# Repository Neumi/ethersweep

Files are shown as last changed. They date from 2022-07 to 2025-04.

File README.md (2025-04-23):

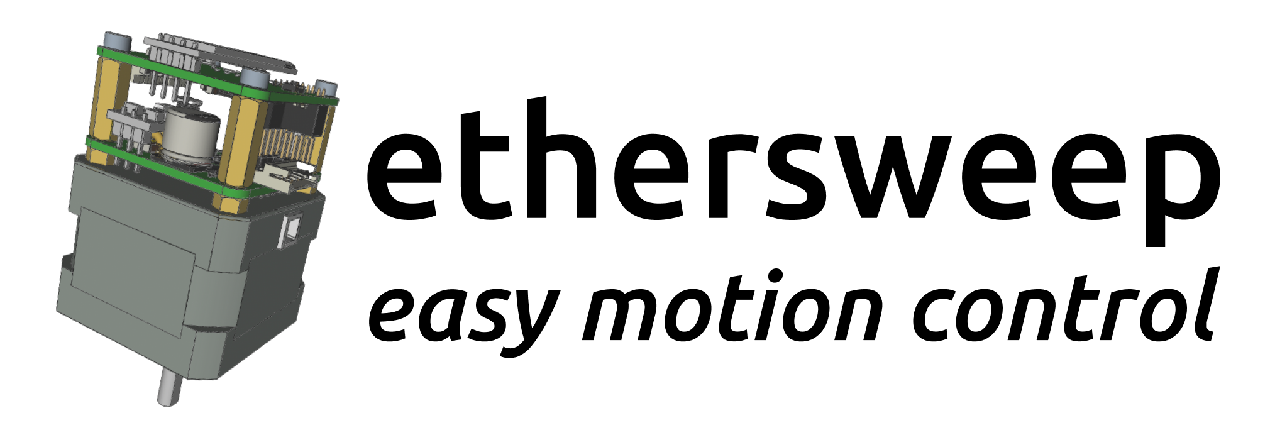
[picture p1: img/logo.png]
Ethersweep Logo


# Ethersweep
### An Open Source Ethernet controllable stepper motor. Easy interfacing with JSON and UDP from any device on the network in any language you choose.

Want to stay updated or participate? Join my [Discord](https://discord.com/invite/rerCyqAcrw)!

*As there is quite some interest in buying a controller, please fill out this form to help me better understand what Ethersweep would be used for https://forms.gle/FLgfvCP1hjCCp2636*

More media/press material:
https://drive.google.com/drive/folders/1qrk8QeEkzJ8hkr-H0x3y7xxhLTKhMb_F?usp=share_link

> *NEWS NOTE:*  Ethersweep is a project still in development. If you plan to order boards for yourself, you can, but expect it to take some work to get everything running! If you have any questions, please write me on Discord: https://discord.com/invite/rerCyqAcrw or
LinkedIn: https://www.linkedin.com/in/neumi/
If you need a custom assembly code or have a special use case in mind, contact me.
The latest running version is in the [production](electronic_design/production) directory. It is now an STM32f103 version with TMC2209 stepper driver. The assembly files contain LCSC part numbers and can be directly ordered at JLCPCB including assembly. Only some THT parts and SMD AS5600 encoder must be soldered by hand.

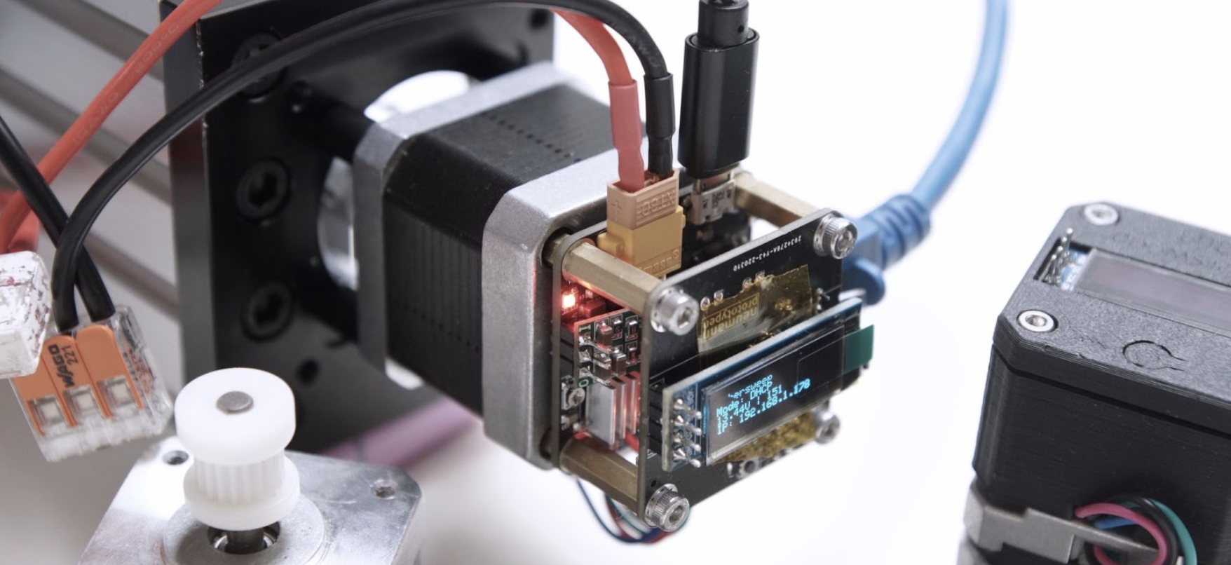
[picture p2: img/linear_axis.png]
linear axis


## What it does
Ethersweep is a motor controller for NEMA17 stepper motors that can be controlled from normal Ethernet networks. This means that you will be able to control motion from normal computers (laptop/server/raspberrypi), mobile devices, microcontrollers, PLCs and any other machine that is capable of sending UDP messages. On top you can control as many motors as you like because every motor gets an IP address from the DHCP server on your network.
You can also connect End and E-Stops to the controller. Sensor data like encoder feedback, voltage, running and button states can also be requested via network requests.

All you need is a network and power between 5v and 30v.
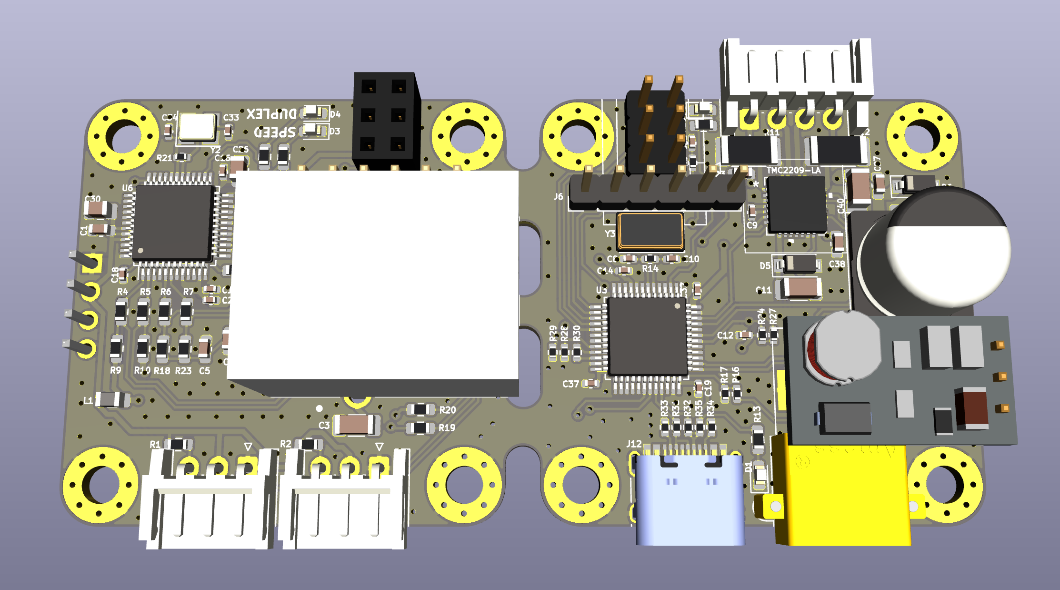
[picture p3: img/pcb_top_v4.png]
PCB Photo


## What it needs
Every motor has to be connected to an Ethernet network (optimally with DHCP) and a power supply between 5...30V. USB can be used for programming the controller with new firmware. End and E-Stops can be connected with JST3-pin connectors. To send instructions to Ethersweep you just send a JSON-encoded message via UDP to the controller's IP and port.

## Features:
- W5500 Ethernet controller
- STM32f103 Microcontroller @ 72MHz
- Trinamic TMC2209 Stepper motor driver
- AS5600 magnetic rotary encoder
- XT30 power connector
- Oled 128x32 Display
- USB programmable
- Inputs for E-Stop and End-Stop
- Reset button
- Fits on a NEMA17 stepper motor
- standard RJ45 network connector

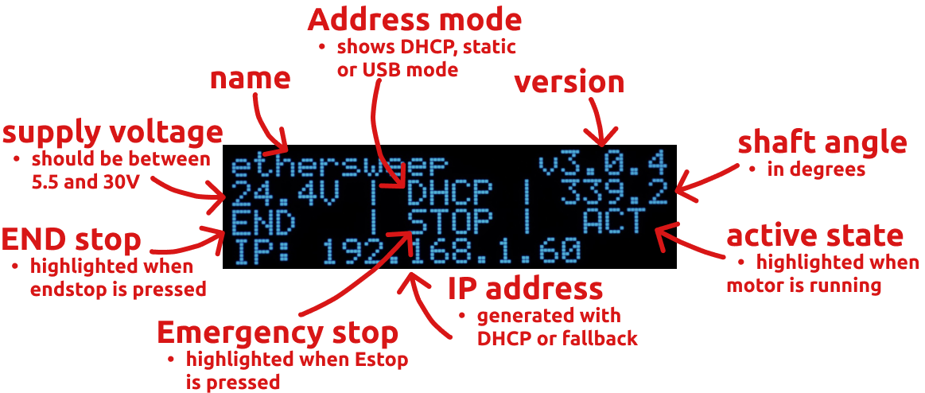
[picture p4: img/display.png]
Display content


## How to get started:
Build an (or multiple) Ethersweep controller. All manufacturing/assembly files work with JLCPCB and only some easy THT soldering is needed when the boards arrive. The code is available in the repository.

Connect your Ethersweep controller to your network via ethernet and connect to a 5.5...30V power source. Stick an encoder magnet (radial magnetized) on a NEMA17 motor shaft and connect the controller to the four M3 screws of the motor.
Once connected to power and Ethernet, it searches for an IP address using DHCP. When an IP is found, the controller shows it on the display and it's ready to use. When no IP is found, it defaults to 192.168.1.111 if available. (It is recommended to use DHCP)

Now you can use the Python script to control the motor.

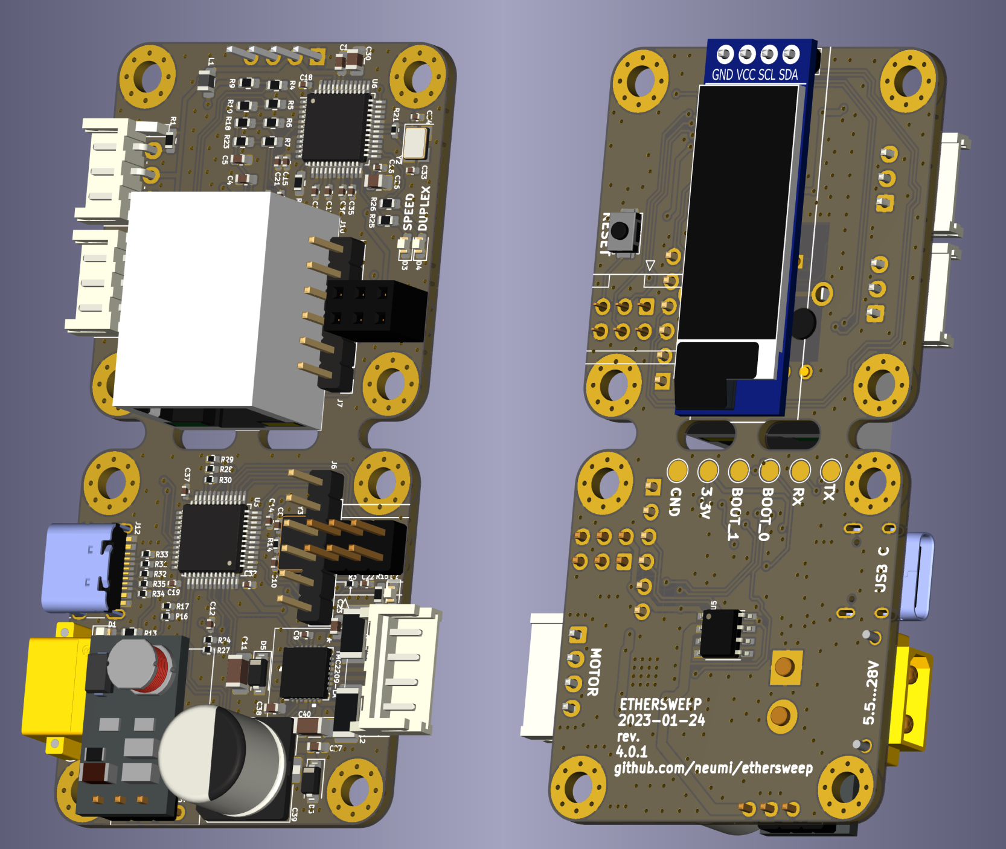
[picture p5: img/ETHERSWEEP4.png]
PCB raw B

cad rotation
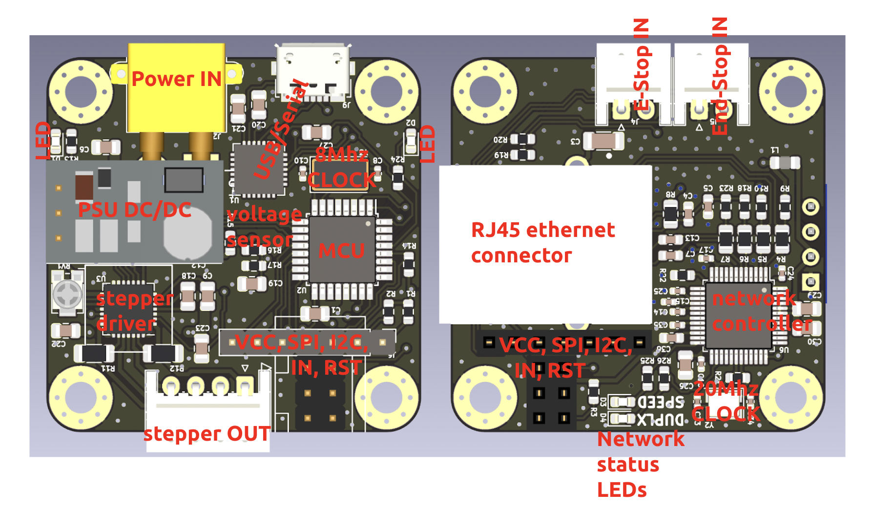
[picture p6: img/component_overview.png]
pcb layout


## Using Python to control a stepper motor:

```python
import socket
import json

IP_MOTOR = "192.168.1.185" # ethersweep IP (change to motors IP)
UDP_PORT = 8888 # ethersweep port

def drive_motor(steps, speed, direction, mode, motor_ip):
    json_data = json.dumps({'steps': steps, 'speed': speed, 'direction': direction, 'mode': mode})
    message = json_data.encode()
    sock = socket.socket(socket.AF_INET, socket.SOCK_DGRAM)
    sock.sendto(message, (motor_ip, UDP_PORT))

drive_motor(100, 9500, 1, 32, IP_MOTOR) # this will spin the motor 100 steps
```

## Video:
LINK TO VIDEO (https://www.youtube.com/watch?v=80j7L1H61Hw)

Follow the project on hackaday.io: https://hackaday.io/project/187187-ethersweep

## Upcoming Features:
- [ ] improved Broadcast mode + motor synchronization for multiple motors
- [ ] motor servo mode
- [ ] TMC2209 software interface
- [ ] scheduler

## Big thanks to the sponsors of this project!
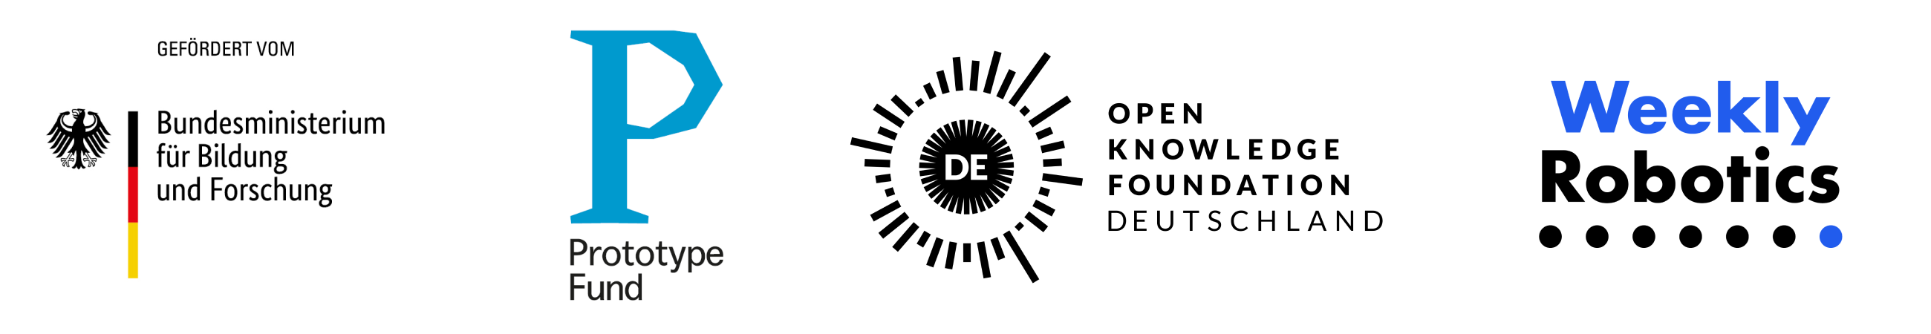
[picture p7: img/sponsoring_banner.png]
sponsor_banner


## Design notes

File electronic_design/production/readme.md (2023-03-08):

# Production ready files

If you like to build an Ethersweep version, check these folders. All versions in this folder are checked and can be ordered from a PCB manufacturer.

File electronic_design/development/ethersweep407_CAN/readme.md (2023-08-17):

# Version 4.6.0

Current development files.

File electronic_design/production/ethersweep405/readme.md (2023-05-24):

# Version 4.5.0

Added CP2102 with STM32f103 and micro USB on a four layer board.
Sent to manufacturing on 24.05.2023

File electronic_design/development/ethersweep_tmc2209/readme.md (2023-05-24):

# Ethersweep with TMC2209

This versions goal was to fix some issues I had with the Atmega328 / TMC2208 version.
I changed:
  - STM32f103 at 72Mhz instead of ATMega328 at 8Mhz
  - native USB support instead of CP2102 serial/USB converter
  - USB C connector instead of Micro USB
  - TMC2209 instead of TMC2208 (Sensorless homing!!, higher current, faster speeds, software interface)
  - 3-pin (3.3,gnd,sig) HOME and ESTOP connectors instead of 2-pin
  - better power design -> less noise

Unfortunately, I made two pretty annoying mistakes. Therefore Ethersweep was not working (old verion 3 boards could be used though) and the TMC2209 didn't work as well. Accordingly this is not a production version. The issues will be fixed in Version 4.2.0.

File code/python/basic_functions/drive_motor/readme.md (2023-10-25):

### Basic Drive Motor Command

Run this command to get an Ethersweep controller spinning. This is a very basic test to run the motor a certain amounts of steps in a certain direction with a certain speed with the option to hold or freewheel the motor in the end.

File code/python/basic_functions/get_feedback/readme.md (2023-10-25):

### Get feedback from Ethersweep

This triggers the Ethersweep controller to send back feedback like voltage, angle and other parameters. It is an asynchronous setup. One is sending requests, the other task receives the feedback from the controller.

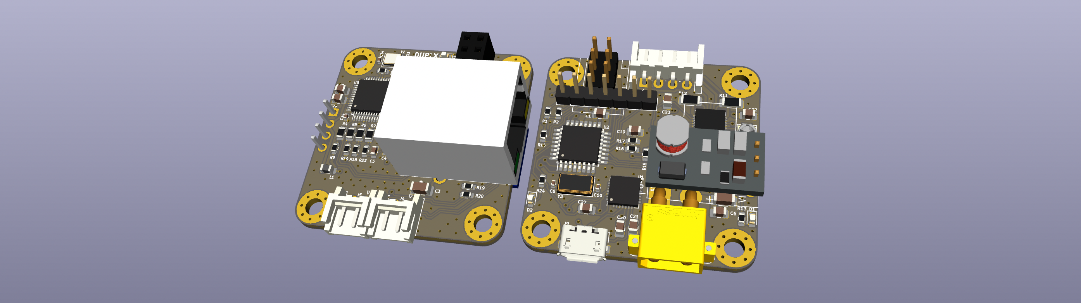
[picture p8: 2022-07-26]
img/3d_side.png

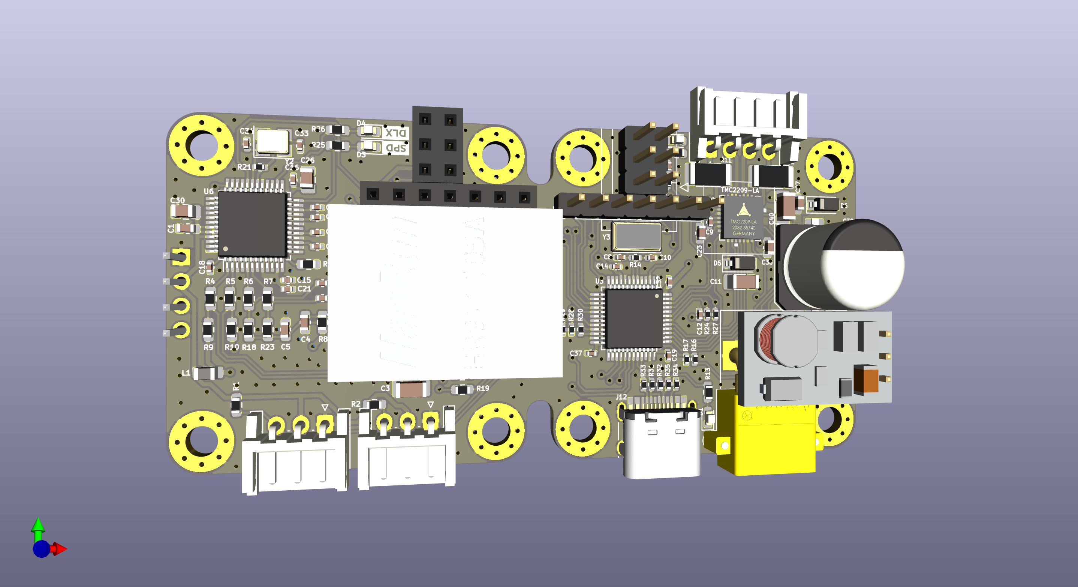
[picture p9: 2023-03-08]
img/rotation/ethersweep_2.png

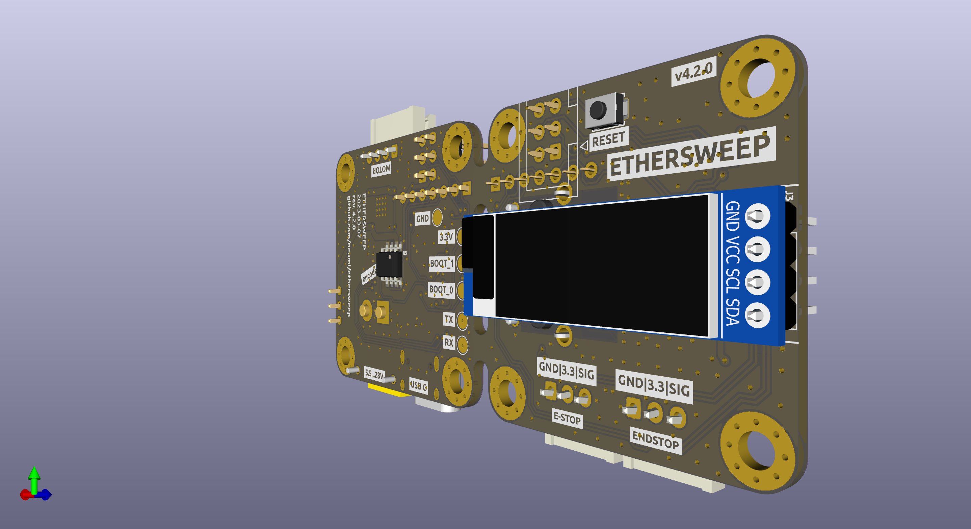
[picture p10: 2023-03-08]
img/rotation/ethersweep_14.png

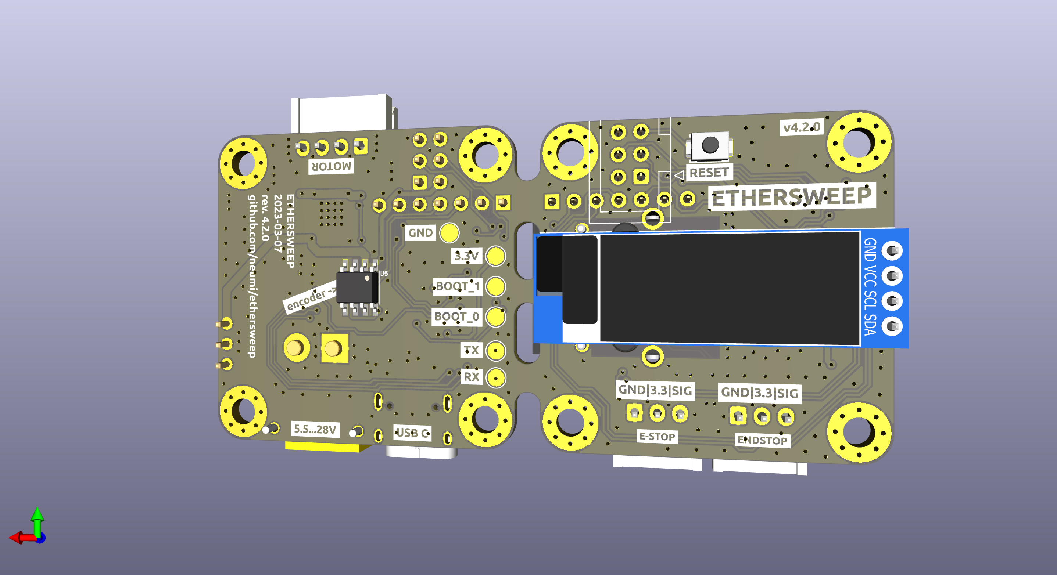
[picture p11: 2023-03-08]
img/rotation/ethersweep_18.png

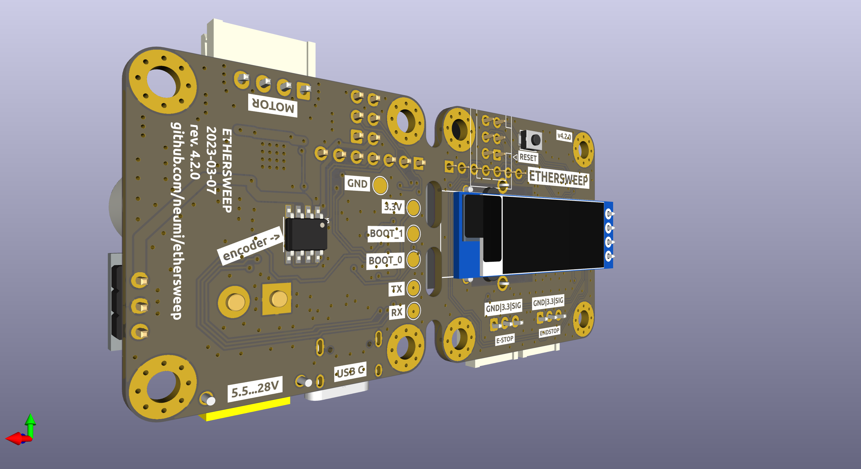
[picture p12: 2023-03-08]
img/rotation/ethersweep_23.png

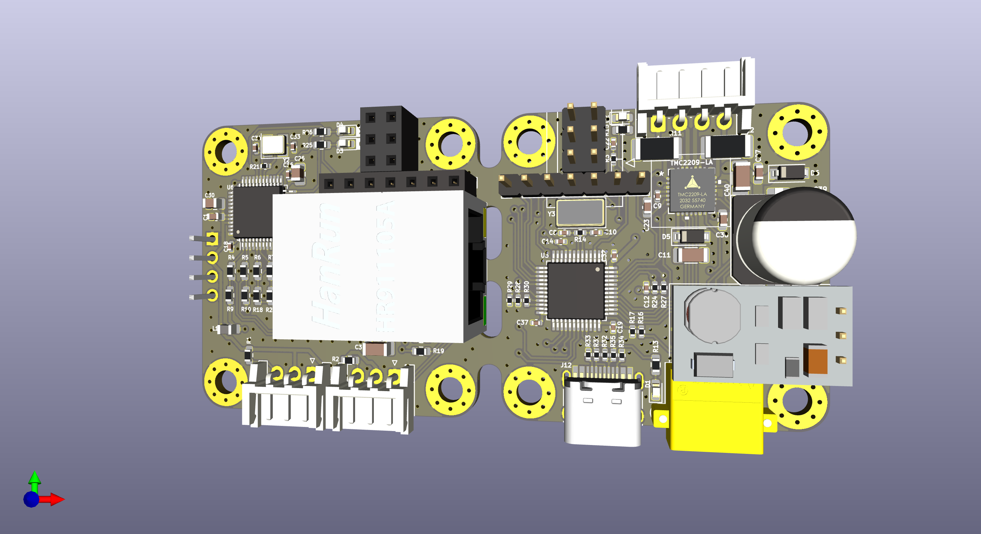
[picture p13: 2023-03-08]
img/rotation/ethersweep_36.png

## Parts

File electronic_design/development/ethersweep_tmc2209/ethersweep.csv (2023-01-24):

Comment | Designator | Footprint | LCSC
C100nF | C1,C6,C23,C27,C38 | Capacitor_SMD:C_0603_1608Metric | C14663
C2.2-4.7uF ceramic | C11 | Capacitor_SMD:C_1206_3216Metric | C29823
C100nF | C12,C14,C15,C16,C17,C18,C19,C20,C21,C22,C32,C37 | Capacitor_SMD:C_0402_1005Metric | C307331
C4.7uF | C2 | Capacitor_SMD:C_1206_3216Metric | C29823
C10uF | C26,C30 | Capacitor_SMD:C_0805_2012Metric | C15850
C1nF | C3 | Capacitor_SMD:C_1206_3216Metric | C35216
C10uF | C31,C40 | Capacitor_SMD:C_1206_3216Metric | C13585
C18pF | C33,C34 | Capacitor_SMD:C_0402_1005Metric | C1549
C10nF | C35 | Capacitor_SMD:C_0402_1005Metric | C15195
C4.7uF | C36 | Capacitor_SMD:C_0402_1005Metric | C23733
C_330uF | C39 | Capacitor_SMD:CP_Elec_10x10 | C249985
C22nF | C4 | Capacitor_SMD:C_0603_1608Metric | C21122
C10nF | C5 | Capacitor_SMD:C_0603_1608Metric | C57112
C6.8nF | C7,C13 | Capacitor_SMD:C_0402_1005Metric | C1542
C22pF | C8,C10 | Capacitor_SMD:C_0402_1005Metric | C1555
C22nF 50V | C9 | Capacitor_SMD:C_0402_1005Metric | C1532
LED | D1,D2 | LED_SMD:LED_0603_1608Metric | C2286
LED | D3,D4 | LED_SMD:LED_0603_1608Metric | C2296
D_TVS_5V | D5 | Diode_SMD:D_SOD-123 | C478011
D_TVS_30V | D6 | Diode_SMD:D_SOD-123 | C553410
USB_C_Receptacle_USB2.0 | J12 | Connector_USB:USB_C_Receptacle_HRO_TYPE-C-31-M-12 | C165948
L600OHM | L1 | Inductor_SMD:L_0805_2012Metric | C1017
R10k | R1,R2 | Resistor_SMD:R_0603_1608Metric | C25804
R100mOHM | R11,R12 | Resistor_SMD:R_2010_5025Metric | C175979
R330 | R13,R19,R20,R25,R26 | Resistor_SMD:R_0603_1608Metric | C23138
R1M | R14,R21 | Resistor_SMD:R_0402_1005Metric | C26083
R1k | R15 | Resistor_SMD:R_0603_1608Metric | C21190
R1k | R17,R30 | Resistor_SMD:R_0402_1005Metric | C11702
R12K4 | R22 | Resistor_SMD:R_0603_1608Metric | C234268
R10k | R3,R16,R24,R27,R28,R29 | Resistor_SMD:R_0402_1005Metric | C25744
R22 | R31,R32 | Resistor_SMD:R_0402_1005Metric | C25767
R5.1k | R33,R34 | Resistor_SMD:R_0402_1005Metric | C105872
R1.5k | R35 | Resistor_SMD:R_0402_1005Metric | C25867
R33 | R4,R5,R6,R7 | Resistor_SMD:R_0603_1608Metric | C23140
R10 | R8 | Resistor_SMD:R_0603_1608Metric | C22859
R49.9 | R9,R10,R18,R23 | Resistor_SMD:R_0603_1608Metric | C23185
STM32F103C8Tx | U3 | Package_QFP:LQFP-48_7x7mm_P0.5mm | C8734
W5500 | U6 | Package_QFP:LQFP-48_7x7mm_P0.5mm | C32843
TMC2209-LA | U7 | KiCad:TMC2209-LA | C465949
Crystal_25MHz | Y2 | Crystal:Crystal_SMD_3225-4Pin_3.2x2.5mm | C9006
Crystal | Y3 | Crystal:Crystal_SMD_5032-2Pin_5.0x3.2mm | C115962

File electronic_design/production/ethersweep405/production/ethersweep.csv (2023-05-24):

Comment | Designator | Footprint | LCSC
C100nF | C1,C6,C23,C27,C38 | Capacitor_SMD:C_0603_1608Metric | C14663
C2.2-4.7uF ceramic | C11 | Capacitor_SMD:C_1206_3216Metric | C29823
C100nF | C12,C14,C15,C16,C17,C18,C19,C20,C21,C22,C29,C32,C37,C41,C42 | Capacitor_SMD:C_0402_1005Metric | C307331
C4.7uF | C2 | Capacitor_SMD:C_1206_3216Metric | C29823
C10uF | C26,C30 | Capacitor_SMD:C_0805_2012Metric | C15850
C1nF | C3 | Capacitor_SMD:C_1206_3216Metric | C35216
C10uF | C31,C40 | Capacitor_SMD:C_1206_3216Metric | C13585
C18pF | C33,C34 | Capacitor_SMD:C_0402_1005Metric | C1549
C10nF | C35 | Capacitor_SMD:C_0402_1005Metric | C15195
C4.7uF | C36 | Capacitor_SMD:C_0402_1005Metric | C23733
C_330uF | C39 | Capacitor_SMD:CP_Elec_10x10 | C249985
C22nF | C4 | Capacitor_SMD:C_0603_1608Metric | C21122
C10nF | C5 | Capacitor_SMD:C_0603_1608Metric | C57112
C6.8nF | C7,C13 | Capacitor_SMD:C_0402_1005Metric | C1542
C22pF | C8,C10 | Capacitor_SMD:C_0402_1005Metric | C1555
C22nF 50V | C9 | Capacitor_SMD:C_0402_1005Metric | C1532
LED | D1,D2,D3,D4 | LED_SMD:LED_0603_1608Metric | C2286
D_TVS_5V | D5 | Diode_SMD:D_SOD-123 | C478011
D_TVS_30V | D6 | Diode_SMD:D_SOD-123 | C553410
MountingHole_Pad | H1,H2,H3,H4,H5,H6,H7,H8 | MountingHole:MountingHole_3.2mm_M3_Pad_Via
AVR-ISP-6 | J1,J8 | Connector_IDC:IDC-Header_2x03_P2.54mm_Vertical
HR911105A | J10 | modules:HANRUN_HR911105A | C12074
USB_B_Micro | J11 | Connector_USB:USB_Micro-B_Molex_47346-0001 | C132560
Conn_01x02_Male | J2 | Connector_AMASS:AMASS_XT30PW-M_1x02_P2.50mm_Horizontal | C431092
Conn_01x04_Female | J3 | Connector_PinHeader_2.54mm:PinHeader_1x04_P2.54mm_Vertical
Conn_01x03_Male | J4,J5 | Connector_JST:JST_EH_S3B-EH_1x03_P2.50mm_Horizontal
Conn_01x07_Female | J6 | Connector_PinHeader_2.54mm:PinHeader_1x07_P2.54mm_Vertical
Conn_01x07_Male | J7 | Connector_PinHeader_2.54mm:PinHeader_1x07_P2.54mm_Vertical
Conn_01x04_Female | J9 | Connector_JST:JST_EH_S4B-EH_1x04_P2.50mm_Horizontal
L600OHM | L1 | Inductor_SMD:L_0805_2012Metric | C1017
R10k | R1,R2 | Resistor_SMD:R_0603_1608Metric | C25804
R100mOHM | R11,R12 | Resistor_SMD:R_2010_5025Metric | C175979
R330 | R13,R19,R20,R25,R26 | Resistor_SMD:R_0603_1608Metric | C23138
R1M | R14,R21 | Resistor_SMD:R_0402_1005Metric | C26083
R1k | R15 | Resistor_SMD:R_0603_1608Metric | C21190
R1k | R17,R30 | Resistor_SMD:R_0402_1005Metric | C11702
R12K4 | R22 | Resistor_SMD:R_0603_1608Metric | C234268
R10k | R3,R16,R24,R27,R28,R29 | Resistor_SMD:R_0402_1005Metric | C25744
R33 | R4,R5,R6,R7 | Resistor_SMD:R_0603_1608Metric | C23140
R10 | R8 | Resistor_SMD:R_0603_1608Metric | C22859
R49.9 | R9,R10,R18,R23 | Resistor_SMD:R_0603_1608Metric | C23185
SW_Push | SW1 | Button_Switch_SMD:SW_Push_SPST_NO_Alps_SKRK | C720477
3.3V | TP1 | TestPoint:TestPoint_Pad_D2.0mm
GND | TP2 | TestPoint:TestPoint_Pad_D2.0mm
RX | TP3 | TestPoint:TestPoint_Pad_D2.0mm
TX | TP4 | TestPoint:TestPoint_Pad_D2.0mm
BOOT_1 | TP5 | TestPoint:TestPoint_Pad_D2.0mm
BOOT_0 | TP6 | TestPoint:TestPoint_Pad_D2.0mm
CP2102N-A01-GQFN28 | U2 | Package_DFN_QFN:QFN-28-1EP_5x5mm_P0.5mm_EP3.35x3.35mm | C6568
STM32F103C8Tx | U3 | Package_QFP:LQFP-48_7x7mm_P0.5mm | C8734
DD4012SA | U4 | modules:DD4012SA
AS5600 | U5 | modules:AS5600
W5500 | U6 | Package_QFP:LQFP-48_7x7mm_P0.5mm | C32843
TMC2209-LA | U7 | KiCad:TMC2209-LA | C465949
Crystal_25MHz | Y2 | Crystal:Crystal_SMD_3225-4Pin_3.2x2.5mm | C9006
Crystal | Y3 | Crystal:Crystal_SMD_5032-2Pin_5.0x3.2mm | C115962

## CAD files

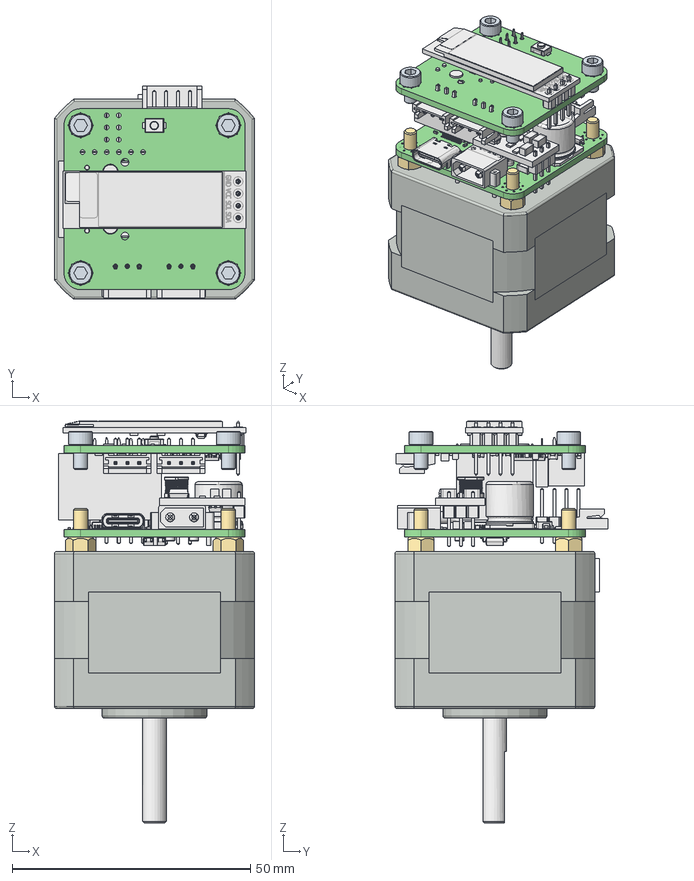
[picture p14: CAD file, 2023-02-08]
3d_files/ethersweep401_assembly.FCStd
42.0 x 44.8 x 84.4 mm
_autosave-ethersweep PCB
_autosave-ethersweep PCB001
standoff_thread1
standoff_thread2
standoff_thread3
standoff_thread4
M3x5mm1
M3x5mm2
M3x5mm3
M3x5mm4
front
back
connector
case
bearing1
bearing2
shaft

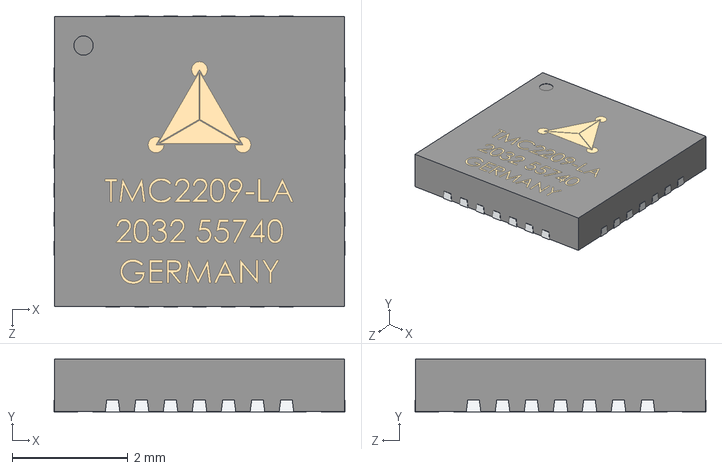
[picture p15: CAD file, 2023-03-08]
electronic_design/development/ethersweep407_CAN/3d_files/TMC2209.STEP
5.02 x 0.911 x 5.02 mm

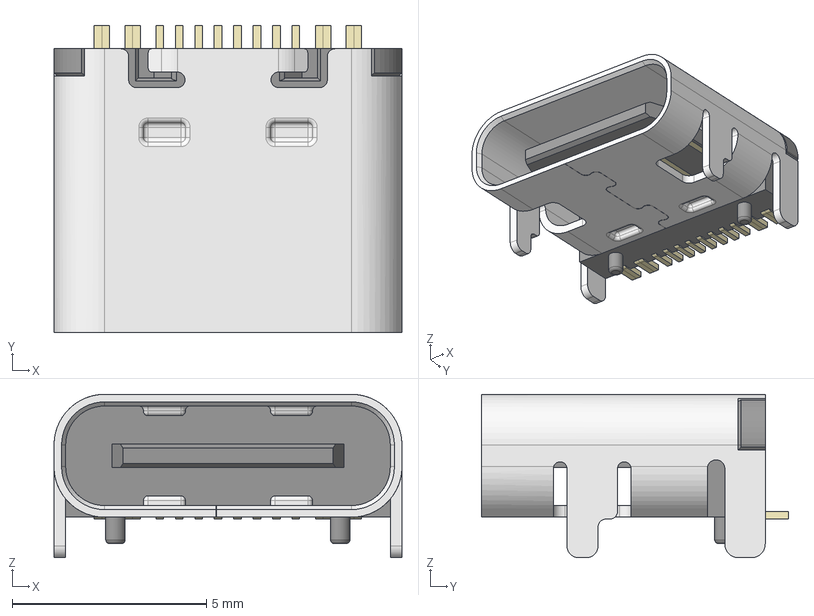
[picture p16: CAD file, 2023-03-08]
electronic_design/development/ethersweep407_CAN/3d_files/HRO_TYPE-C-31-M-12.step
8.95 x 7.90 x 4.20 mm

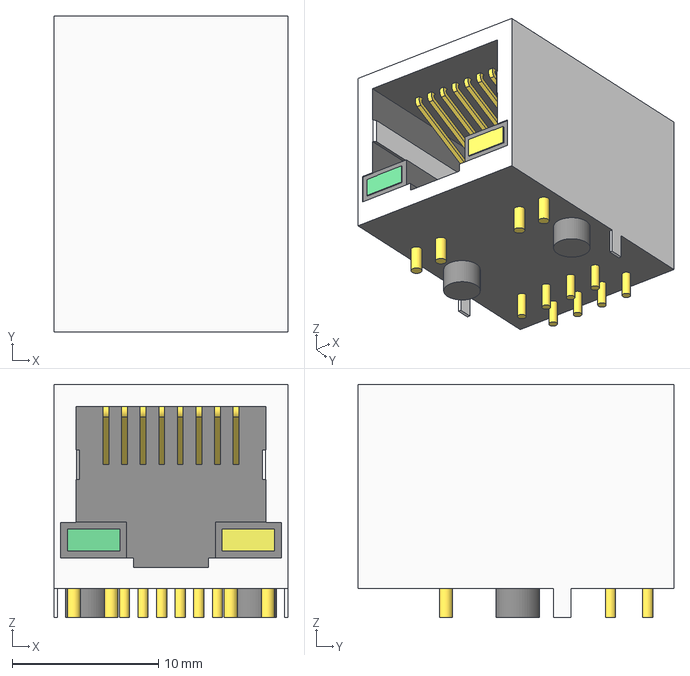
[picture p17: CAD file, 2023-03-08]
electronic_design/development/ethersweep407_CAN/3d_files/HR911105A.step
16.0 x 21.6 x 15.9 mm
contact x 8

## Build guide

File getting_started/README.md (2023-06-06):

Ethersweep Logo

# Getting started with Ethersweep (Still in development)
### How to get started...
### This only works on the current development version 4.5.0 of Ethersweep hardware. It is intended to find and debug hardware issues.
The code is compiled and uploaded using the Arduino IDE with stm32duino installed. Check [this](https://github.com/stm32duino/) to install. (Add this link 
```https://github.com/stm32duino/BoardManagerFiles/raw/main/package_stmicroelectronics_index.json``` 
to the Arduino IDE board manager)

Set these settings under 'Tools' in the Arduino IDE:
![Board settings STM32 Ethersweep](./img/board_settings_STM32.png)

# Get the motor spinning
To test if the motor is connected properly you can run this [code](https://github.com/Neumi/ethersweep/blob/master/getting_started/code_for_testing_v450/motor_test/motor_test.ino).

The motor should spin in different directions with different speeds.

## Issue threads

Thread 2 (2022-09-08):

POE support?

pylogger-html, 2022-09-08:
Really nice project. I've been looking for something like this for a while.

I know you're short on space, but did you consider adding POE support? You can get modules that do most of the work for you (Ag9912 or Ag9924) and you might be able to squeeze one in between the two boards with some longer standoff connectors.

The other thing I was wondering is why you didn't use a 4-layer PCB. The cost increase is fairly minimal these days (looks like jlcpcb adds ~$2-$3 per board for qty=5, but most of your cost is in components) and your signal routing would be a lot cleaner. For signal integrity it's always helpful to have one continuous ground plane layer, although you ended up achieving almost that on the flooded back layer.

Neumi, 2022-09-08:
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

Actually... the POE module might just fit on the top board :D

TheZothar, 2022-09-08:
I too am interested in POE :)  Although i'm also familiar with feature creep in prototype designs and how it can distract for the core goal. Great work so far, looking forward to updates.

gpdaniels, 2022-11-22:
Another +1 for PoE. I'm working towards automating my house and I'm keen to be able to make blinds/curtains/shutters move. I can get PoE to the windows but finding PoE blinds in the UK is a nightmare.

Really finding PoE for most things smart home is awkward. My current plan would be to use a PoE splitter to extract the power and then something like this project to control a stepper. Obviously this won't be the smallest or cleanest solution. Otherwise my options are something like [this olimex board](https://www.olimex.com/Products/IoT/ESP32/ESP32-POE/open-source-hardware) and a stepper driver board.

burner-, 2023-10-08:
poe++ will deliver 70W and instead of doing DC-DC conversion for all power maybe you can use that poe voltage directly for motor and step down only control voltage. Naturally you will need high voltage driver chip for that.

vaughnmonkey, 2025-02-12:
another +1 for POE it would go a long way to cleaning up and simplifying the wiring for any project using these drivers

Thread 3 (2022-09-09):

Higher voltages

MortarArt, 2022-09-09:
Apologies if this is not the correct way to ask a question of the project team. What modifications would be required to allow this to be used with a higher voltage power supply & a larger stepper motor, like a Nema34?

Neumi, 2022-09-09:
Hey! Thanks for the issue. Currently, I use a DD4012SA and the TMC2208. So the input voltage limit is currently at around 36V, but for safety kept at 30V. When updated to TMC2209, the max voltage will drop to 29V. What voltage do you need?

mzilly02, 2022-09-09:
For running a Nema 34 stepper you'll need a tmc5160 with 48v, minimum...

MortarArt, 2022-09-10:
As mzilly02 pointed out, 48v is the starting point really for a nema34. Though, the higher the better for high speed applications. I'm only currently looking at low speed work, so 48v is what I'm aiming at since it's a little safer.

printplaatreparatie, 2022-10-13:
Coincidentally, 48v is the most used PoE (#2) voltage...

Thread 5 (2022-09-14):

Display invert on endstop active strange behaviour

Neumi, 2022-09-14:
Display shows inverted fields on voltage and angle when endstop pin is pressed.

Closed 2022-09-14.

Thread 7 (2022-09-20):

Update arduino json to version 6

Neumi, 2022-09-20:
Currently the code only runs on [arduino_json](https://github.com/bblanchon/ArduinoJson) version 5. This has to be updated. Might also improve performance.

Neumi, 2022-09-21:
fixed in https://github.com/Neumi/ethersweep/commit/cf9fb6df6877794909f1da2bef78e4398f72a58c

Closed 2022-09-21.

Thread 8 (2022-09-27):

fix JLC CPL files

Neumi, 2022-09-27:
Every second update of JLCPCB services crashes the CPL and or BOM files. This might be fixed in the CSVs or in kicad.

Neumi, 2022-09-27:
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

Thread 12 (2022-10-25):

Rethink connectors

Neumi, 2022-10-25:
Micro USB -> USB C
Sensor/EndStop/Estop connectors should be 3-pin with gnd, vcc and sens

Neumi, 2023-01-10:
solved in b0e6d4570277644a2024a451aca1ad1c1fe78cdb

Closed 2023-01-10.

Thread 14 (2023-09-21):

NTP time synchronization for parallel movements of multiple motors

Neumi, 2023-09-21:
Use NTP (or similar) synchronized time to run actions at before defined time points.

Duckle29, 2023-09-21:
I just saw this pop up on youtube and it's interesting.

I think you'd want to use a setup that supports [IEEE 1588 PTP](https://en.wikipedia.org/wiki/Precision_Time_Protocol) which is a way to synchronize clocks on a network to sub-microsecond level.

It requires a phy that supports it, and I'm unsure if the wiznet phy+mac supports it.

One approach could be a new version of this that uses an [STM32F107xx](https://www.st.com/en/microcontrollers-microprocessors/stm32f107vc.html) which has a built in Ethernet MAC with 1588 support. (However the support seems weirdly undocumented from [a quick google](https://community.st.com/t5/stm32-mcus-embedded-software/where-is-the-stm32f107xx-ieee-1588-ptpd-package/m-p/343933))

I'm unsure if the phy also needs support for this, but something like the Ti [DP83640](https://www.ti.com/lit/ds/symlink/dp83640.pdf) Does implement it. ([Ti AN-1729](https://www.ti.com/lit/an/snla099d/snla099d.pdf))

Duckle29, 2023-09-21:
I did some more digging on the F107, and it does seem like it'd be a fair bit of work to implement, but seems fun. I found [This TCP/IP stack](https://andybrown.me.uk/2013/07/14/stm32plusnet/) that supports it

Neumi, 2023-09-22:
This is some valuable information. I also thought a bit about using an STM with built-in ethernet, but in the end didn't find a good solution to the hardware layout. The W5500 sits on the top board and only SPI has to go through the pin headers. Sending the ethernet lines through them wouldn't work I suppose (+ EMI/EMC problems). The other option would be to have the uC on the top board as well and route everything else down. But then the space on the top board is pretty much gone.
But would be worth a try! I always wanted to play around with the built in Ethernet and CAN stuff anyway! :D
Replacing the W5500 would of course be no problem. I choose it because it is widely used, has good drivers, is cheap and everywhere in stock. (I also didn't want to take a deep dive into networking + physical layer stuff :D) I might make use of the hardware interrupt pin (pin 36 on W5500) to get better packet timing. This is currently just connected, but not used in software as for now. This might help with some latency issues (at least the latency that originates from the uC code doing something else ;)).

Duckle29, 2023-09-22:
Yeah, honestly doing the digging on the F107 it seemed cool.... and a LOT of work :sweat_smile:

Neumi, 2023-09-26:
I just checked the F107.... It would be very hard to get them on one board without double-sided assembly. And even with double-sided assembly the THT RJ45 and the F107 would not fit side by side on the board. But I would like to keep the THT RJ45 for stability reasons... The F107 with a smaller form factor like some BGA would be great :D

PhilCowley, 2023-10-05:
To get synchronised movement, could you not try a two stage solution. First send the requested position/speed etc. to each motor, then, once all the motors are ready, send a broadcast "go" signal? This would remove any requirement for an NTP server on the network and any requirements to update RTCs in the controllers.

Duckle29, 2023-10-05:
I haven't really looked in to this more since, but I did brush by some comparisons of hardware PtP like that (very expensive) Ti phy does, compared to software only PtP.

Might be much more interesting to see what kind of sync you can achieve with just a software solution?
I found this: https://github.com/mpthompson/stm32_ptpd

asteppke, 2023-10-13:
Just as a reference for the discussion: With a direct Ethernet connection without special hardware and using NTP one can expect synchronization accuracies below 1ms. For many motion control tasks this is already sufficient. Servo PID loops for example often run with 1 kHz.

With PTP in a pure software mode one can achieve accuracies below 10us, and with dedicated hardware below 100ns.

The effort of a software NTP client implementation is quite small, even from scratch. A dedicated hardware approach looks like overkill here. If there is an easy to port PTP software client that might be beneficial but NTP would cover a lot of potential use cases.

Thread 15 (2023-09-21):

Consider using internal voltage reference

Duckle29, 2023-09-21:
Quick look through the schematic I noticed your voltage reading assumes a 3.3V ADC reference voltage.
Just be aware that your ADC measurements are then limited to the accuracy of your supply voltage.

You probably don't need any high accuracy ADC measurements, I just recently ran into a problem where I did and I wished I'd prepared my PCB for it instead of having to do a re-spin.

The STM32F103 (and F107) have a built in 1.2V, 100ppm/K. It is however +5% -3% for initial accuracy going with the min/max spec so, meh.
I don't have any experience with how close to the typical 1.2V it usually is.

Alternatively an external vref could be used.

Also, remember to check the errata for the MCU you're using when considering this stuff... Yes I also got burned there :P
(The F103 doesn't seem to have any vref related errata, tho a short blurp about ADC ch0 generating a 10ns 150mV blip in certain usecases)

Neumi, 2023-09-22:
Thanks for the tip. I will check for the next hardware version. The ADC is currently only used to detect the raw input voltage (5-30v). I think it is okay to have a drift of a few percent. This is not critical to the operation.

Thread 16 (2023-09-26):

TMC2240 upgrade (maybe)

Neumi, 2023-09-26:
has higher output current and voltage, very compatible to tmc2209

DrechselAdrian, 2023-09-26:
Has even more advantages which could help improve the controller over all. For example Step detection prior to your magnetometer detection on the shaft.

Neumi, 2023-09-26:
I think so too. But I have to read a bit more of the datasheet. But I think its very advanced and might be a good replacement for the tmc2209. They're just bringing out too many new fancy controllers too fast :D

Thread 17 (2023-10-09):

EtherCAT option

mgaffigan, 2023-10-09:
Hi! Love the project.  I saw some comments on the YouTube video which included your view on EtherCAT as

> EtherCAT is closed source. You have to buy the IC/ASIC from Beckhoff for approx. 20€ p.p. You also have to buy product into the EtherCAT community. (Nothing for an open-source project). Ethercat is on a lower Ethernet OSI layer and can, therefore handle requests much faster before it is even decoded. Also you need specialized switches and routers. All of this makes this hard to use and expensive, if you just want to setup a tiny experimental assembly. Of course, if you need very deterministic/hard timing you could/should use i.e. Beckhoff servos. But they are 500€ pp + switches + very expensive cables ... And if you have limited space (robot, small machine) you don't need the big distribution boards etc. A cheap BotBlox switch is enough ;)

While I can certainly understand that viewpoint, I'm opening this issue in hope I can persuade you.  Offering an EtherCAT model solves a couple of  issues that are otherwise challenging in machine builds:
1. Addressing<br/>Since slave addresses are based on cabled positions, no DHCP or IP configuration is required.  You plug your topology together and can address it based on how it is connected or via MAC.
1. Cabling and switching<br/>Since slave IC's include a two or three port "switch", no dedicated switch is required (daisy chaining)
1. Reliability in the face of excess traffic<br/>Due to EtherCAT's mailboxing design, a slave cannot be overwhelmed in the same way that a Microcontroller reading UDP other packets can be.  The ASIC also offloads much of the complexity, allowing a lower cost micro to deliver better functionality.

The LAN9252/LAN9253 is regularly available for less than $10 (+ a second magjack) and replaces the cost of the ethernet MAC.  I imagine this would also cut the microcontroller and OLED cost, and reduce firmware complexity.

The ASIC is the only licensed component.  There are no special cables.  Switches are not required since each slave is daisy-chained.  Routers are not relevant, since it is not a routed protocol.  There are $0 and open source controllers available for Windows and Linux ([1](https://openethercatsociety.github.io/), [2](https://gitlab.com/etherlab.org/ethercat)).

There are, of course, other benefits:
1. Time synchronization
1. Interoperability with PLC's, other controllers, and other motors
1. Safety without secondary cabling

I'm not associated with Beckhoff or any similar EtherCAT manufacturer.  I've just been burned a couple times by Ethernet embedded devices that have tried to re-implement their own automation protocol, and each time have been burned by addressing or communication reliability.  EtherCAT and CANBUS are dominant due to their merits.

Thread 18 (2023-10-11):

Design feedback

pylogger-html, 2023-10-11:
I just saw the youtube video you posted and it looks like you've made a lot of good progress on this project. I decided to check out your schematic/layout and here's some feedback. I just did a quick review of it, so if I got an old design let me know (I went dev and the latest "complete looking" board).

I did not review the firmware, but I do have some STM experience so maybe I'll be inspired to do that later.

* You should start using 0201 components for all your smaller cap's (anything below 100nF) and small resistors (pull-ups, 0 ohm jumpers, etc). Most fab places do not charge extra anymore for this size (jlcpcb hasn't for several years) and those parts can be cheaper sometimes than 0402's. I realize reworking 0201's is tough, but for all the little bypass caps you probably won't be reworking those. Plus the design seems more refined now.

* 100mil is standard for headers, but they do make 50mil headers. Might save you some room if you're doing a multi-board thing (you make the LCD board right?)

* Kicad now supports multiple sheets in version 7.0, so you could split up the schematic into logical blocks (maybe power, uC/com/display, motor control). The board isn't too complex though, so it's kind of a toss-up.

* The routing around C38 is really tight, but you have tons of room on the back layer below it. Same with the motor controller (C40, D6, D5, C11 could all go on the back side. keep the 100n bypass caps on the same side)

* J2 didn't load for me, but is this just a 2-pin terminal block? (the green connectors with screw adjusts)

* Do you really need an 8MHz crystal? The STM32 has a decent (+/- 2% over full temp range) RC oscillator called the HSI that runs at 8MHz. This would save you a bit of cost and a "giant" part in the middle of your board.

* If you want an easy flashing header that adds zero cost, look into tag-connect. Another option would be writing a little bootloader in the STM32 that has just enough code to do ethernet IO & flash memory. Then you could do all the programming entirely with ethernet (you flash the bootloader via a header, then upgrades are done via ethernet).
** To do this you can create a separate linker file and relocate your code somewhere else in memory. The STM32 will boot into the bootloader, the bootloader will check the "upgrade image" and if it's okay boot from it. Then you just need a mechanism to revert back to the upgrade image if needed (push button maybe?)

* You should look into adding ESD/EMI protection to all exposed ports and accessibly supply rails (probably 5V, must you can skip 3.3V). There are single chip options for USB and you'll need them for the stepper motor driver. The TMC2209 has example protection circuitry in the datasheet that you should have. Aim for at least 16kV rating on the ESD stuff (32kV would be better, but it isn't required).

Crazy ideas:

* Switch to USB-C for power and get one chip that drives the CC1/2 lines so you can get 20V via USB power delivery. Yeah, I know it's not 28V, but the new USB PD standard supports 28V/36V/48V at up to 5A. You can still use the DP/DM lines for the UART. I can't find the chip right now, but this board has a 20V version (I'd guess the new PD chips will be around in ~3-6 months): https://www.amazon.com/JacobsParts-Voltage-Trigger-Module-Type-C/dp/B0C7JMX9HS/

* I know you just switched to a new uC, but have you looked at the RPI Pico? It has a dual core M0 running at >100MHz and it's cheaper than the STM ($0.97 vs $1.41 at JLCPCB, although you'll need a crystal & flash for it - so probably same cost). The C/C++ API for the RPI Pico is really well tested and you can probably port a lot of code. No motor controller though, so you'll probably need to dedicate one core to the motor/feedback sensor.

Neumi, 2023-10-11:
Very good and valuable feedback. Makes sense to me and I will change it on the next version.

The RP2040 might be a good candidate. I only knew it running micro python and didn't like it. Having two cores with C++ would actually be very beneficial for the motor control.
USB PD was on the list of requests but I didn't want too many chips/complex parts on the board for now and keep them all on one side for cost reasons. Maybe this could change in the future. (but for now, keep complexity low)
The Ethernet software update would be very cool. But it should be easy to understand and doable for the average maker.
ESD/EMI protection was not really taken care of due to a lack of knowledge and testing equipment.
Tag-connect is cool, but I think having USB is also cool if you only need to run one Ethersweep controller from your computer. Not using the USB/Serial bootloader feels like a waste of potential.
A 2% oscillator would most likely be okay. It might be good to free up some space.
The pin headers have to be 16mm long. I'm not sure if you get them with the low pitch. So I kept the normal ones.
J2 is an xt30 connector. Standard in RC copters and planes and some motor controllers. Maybe this could change to a more professional/strain-reliefed connector.

Thanks again!

gchenfc, 2023-10-11:
Just a quick note on RP2040, IIRC its ADC is not super great; something like 1 hardware ADC multiplexed to 3 pins and low bit resolution.  I haven't looked at your stepper driver code to see how much real closed loop servo control you're doing, but I did see you have a pair of shunt resistors so the RP2040's ADCs might not be suitable depending on the accuracy you're targeting.

Also would like to upvote the ESD protection - adding protection and ideally opto-isolating anything going in/out.  Not sure about the projects you typically do, but in my medium-sized projects, anything without opto-isolation of communication ports always blows up eventually due to EMI & ground loops.

And this is an unrelated comment, but I personally would love to see (eg in README's):
* timing precision / latency + reliability (# packets lost) tests, ideally with e.g. 3 motors running simultaneously, including with motors enabled since EMI is presumably significant
* rough bandwidth figures you'd be able to achieve - I assume 100Mbps ethernet so maybe 250Hz or something?  Not sure
* a rough JLCPCB cost estimate in one of the README's would save the trouble of uploading the zip to jlc to investigate whether I want to more seriously consider trying out a run of these boards
* schematic & board pdf's uploaded to github, so I can do a review without cloning :)

pylogger-html, 2023-10-12:
Yeah, that's a good point about the ADC. You can improve the accuracy a bit (https://youtu.be/F0o1C7nEgw0?si=pLa2Wp7sBuP2In6G&t=422), but still the number of channels is kinda rough compared to the STM32.

Getting the UART output working with the RP2040 in C/C++ is super easy and you can redefine the USB descriptor if needed (vid/pid/sn/description can all be redefined with pre-processor macros).

I agree that Opto-isolators would be great, but it'll be tough to do that for every stepper motor signal. RX/TX are easy, but then you have the analog signals to worry about (current shunt voltages, power supplies, etc). Totally doable, but you'll probably have to totally redo the layout.

Couple more items:
* You're using a ~300uF aluminum capacitor which I think has <1A ripple current rating (my translated datasheet for the part could be wrong), but you're probably using more than that to drive the stepper. Aluminum polymer caps can do 5-10x more current, they're more reliable, have better failure modes, but they cost more. You can probably get away with a bit less voltage de-rating too (I have a commercial design with 35V alum-poly caps running at 33V). The DC current isn't the issue here, but the instantaneous peak current you're getting from the cap and how often that happens.

SW - STM32 code
* wow, I didn't realize arduino like stuff would run on the STM32. I thought you'd go the STM32IDE & STM32CubeMX route, but a networking stack would be a challenge. I don't do much work with this API, so I'll skip this.

SW - I looked in python on the master/main branch
* You've got your venv in version control (venv should always be in your .gitignore and never in a commit). You should have a setup.py for your project or requirements.txt to build your venv. You can do "pip freeze > requirements.txt" to generate this and it'll help if anyone else runs this. I like to do some had refinements of mine to just have the few high level packages I actually need and let the maintainers deal with dependencies.
** pycharm should recognize these files once you have them and it'll make setting up your project on another machine really easy.

* I recommend making an "ethersweep" python package that has a central class object and member routines that abstract the details of sockets, command formating (json, url's, etc). For development you can install this as a local editable module with "pip install -e ." provided you have a setup.py. Your code would then do something like this:

from ethersweep import ethersweep
foo = ethersweep()
foo.connect(ip=192.168.1.55, port=8888)
foo.info() # returns motor SN, sw/hw rev, maybe a user configurable name
foo.getpos() # returns the stepper angle
foo.hold() # holds current position
foo.getStatus() # returns currents/voltages
foo.setpos(angle=33.3, angPerSec=0.1) #you can use **kwargs to define several possible parameters, like deltaAngle, absAngle, moveTime. This way you don't have a ton of required parameters)
foo.close()

* Once you have this basic framework going, you'll need automated tests (to test python & your firmware). I like using pytest and I can give you a ton a tips when you get to that stage.

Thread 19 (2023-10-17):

Daisy chain connection

LukasM937, 2023-10-17:
**Note:**
This is purely an enhancement Idea.

**Idea:**
In my opinion the addition of a second RJ-45 port, along with the necessary switch on the PCB - or an Additional board - would improve the longterm usability, since it would make it possible to daisy chain the servos.

**Reasoning:**
- Daisy chaining and on device switching would ease up wiring in most cases.
- cleaner cable management specially for larger setups could be achieved.
- It would negate the necessity to use an external switch.
Thus it would ad the possibility to run it from a usual SBC - like the RPi-4 or similar - as these often only have one RJ-45 port.
Further it could improve runtime for remote controlled robots - since the number of consumers are reduced.

**Possible issues:**
- It would take a lot of space on the PCB, that already seamed to be crowed.
- The extra cost in research, engineering, manufacturing might not justify the benefits for simpler setups (cables and routers are cheap)

Neumi, 2023-10-18:
Cool idea. I also played around with the thought.
But as you said, space is a big problem. It could be possible with double-sided assembly and maybe throwing out the w5500 LQFP package and replacing it with a smaller IC. As a switch IC, it could be the KSZ8863 as an option. But it's quite expensive (5-10€) and has a large LQFP-48 package as well.
And I'm not sure how the daisy changing of switches would affect the latency on the last controllers... most likely not so great.
But it's worth an experiment, I'd guess! It could also be just a replacement board for the current networking/display boards, as the only other functionality is the Display, reset, Estop and Endstop.

I think another great option is always a botblox switch. They're actually the exact same size as Ethersweep and have 5 ports available. (even with POE (might be cool for the future)).

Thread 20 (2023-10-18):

build scheduler

Neumi, 2023-10-18:
Different tasks have to run at the same time. Like: Display refresh, sensor refresh, motor drive, network buffer fetch ...
Build a scheduler that knows about different priorities in different situations/modes and do the associated tasks accordingly.

Change the architecture accordingly. Don't break too much old code please. (but also make it future proof)

see https://github.com/Neumi/ethersweep/tree/scheduler

Closed 2023-10-25.

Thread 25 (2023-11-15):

Any plans for Nema 23 ?

ajay01994, 2023-11-15:
Hi ,

Thanks a lot for making this project available to all of us ,indeed quite a lot of handwork goes in making such projects , and any such work is highly appreciated , however do you have any plans to make ethersweep  for Nema 23/24 closed loop motors ?

Neumi, 2023-11-27:
Plans yes, but not in the making currently. In the end it would be a very small hardware change (as long as I keep the input voltage range the same). Bet I'm not sure about the stepper driver yet. TMC2209 is a bit too weak to drive nema23/24.

Neumi, 2025-02-03:
@luzpaz Hey, currently, there is no progress in that direction. I'm currently mainly working on other projects and can't invest enough time into a new hardware version. What do you need it for if I may ask?

luzpaz, 2025-02-04:
Thanks. Just curious.

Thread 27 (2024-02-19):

pdf schematics

wolfgangr, 2024-02-19:
I just tried to open your kicad files, but it fails with lots of libraries missing.
Most IC's just show up as "??"
maybe it's fault of my old debian 10... anayway...

would be great to have a schematics drawing as a pdf, without any elaborated dependencies to be fulfilled

-----------

btw
I'm just in the process to order some (~10 ) units.
anybody interested in bundling order volume?

Neumi, 2024-08-12:
Sure good point! I'll see how this could be improved. I think there are actually some local dependency issues in the repo. I need to look into that.

The Discord server is a good place to ask for bundling orders. If you're located in Germany / Europe, write me a DM on Linkedin or Discord. I might order new boards in the next weeks. @wolfgangr

wolfgangr, 2024-10-28:
sorry for the late response - sometimes live comes into the way....

I've moved my focus to grblHAL now and consider a solution with linear encoders, so the loop includes mechanical backlash as well. But even this runs at secondary priority and is stalled at the moment.

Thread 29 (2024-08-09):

DCHP + Other Setup teething problems

TGiles1998, 2024-08-09:
Hi,

I've been really struggling to get this to work.

I've got the hardware built at JLCPCB. I've built five of them to ensure it wasn't a hardware problem.

Initially SPI from the STM32-F103C8T6 to the W5500 wasn't working but have now got that to talk.

It's now all failing on setting up the DCHP.

My ethernet cable works and I've tested other things. Were there any teething problems you experienced in setting this up and how did you overcome them?

Should this code on VSCode with platformio just work or did you have to do other things?

many thanks,

Thomas

TGiles1998, 2024-08-12:
@Neumi

What would you recommend to only allow for static IP to work?

Neumi, 2024-08-12:
Hi @TGiles1998
It's great to hear that you already have the hardware on your desk and that the ordering process went OK! (we had some issues with that in the past)
The code and VScode files should be enough to tell VScode what dependencies it needs to load.
- does the code compile without errors?
- do you use external power? (like 12v 1A)
- are the boot pins connected correctly? (BOOT_1 = floating, BOOT_0 = HIGH (3.3V) for upload, BOOT_0 = floating, BOOT_1 = floating for running code from STM32 flash)
- try to restart the board without the USB being connected. Sometimes, I had issues with the W5500 not starting up / working properly when USB was connected (I am not sure where this error comes from, as they don't really need to interact). Usually, this error made the RJ45 LEDs flash in strange patterns.
- I had better experiences with DHCP, but this might also be an issue with the DHCP server/router. Some don't like fast MAC address changes (happens with Ethersweep after firmware change, when FLASH erase is enabled)

I still need to work a lot on the documentation, and this info has to find its way into that. I'm sorry that it's currently not as straightforward as it would ideally be!
Please keep me posted if the problem is solved or if you need further assistance!

TGiles1998, 2024-08-13:
Hi @Neumi,

Thank you very much for your reply.

I've further debugged the hardware and there were some issues on signal quality between the two PCB halves, for my hardware at least it seems.

I've been adding a lot of debugging flags into the code to try and identify issues. I've now got the LINK to be okay, so communicating with the W5500 is happy, but it just fails to setup DCHP and/or STATIC.

I think this could be due to issues with the external ethernet library, for the bluepill_f103c8, that I've tried to debug and change.

I think I'm going to use a different hardware solution for what I'm after now, but can try new code if it gets changed on the repo.

I've attached some pictures and I hope they help.

many thanks,

Thomas

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

Neumi, 2024-08-13:
Ok. Interesting error. Maybe check if the voltage converter is up for the task. Is there a reason to use a linear voltage regulator instead of the buck converter I liked in the repo? The W5500 draws quite some current.
Run the automated hardware tests to check if everything else works and maybe try the W5500 library examples without the rest to narrow down the problem.

TGiles1998, 2024-08-17:
Hi @Neumi, the linear voltage regulator is being used as I couldn't source your buck converter anywhere with a reasonable lead time and other buck converters I then used for 24V to 3V3 died when I had to put boot_0 to 3V3 when programming as it just shorted stuff out haha, I've now tried simply putting a 24V into the 28V line and a separate power supply for 3V3 but to no luck unfortunately, I've checked all the cross PCB signals and they are all good. Some weirdness is just occurring with the Ethernet for some reason. I'll let you know where I get to with continued debugging.

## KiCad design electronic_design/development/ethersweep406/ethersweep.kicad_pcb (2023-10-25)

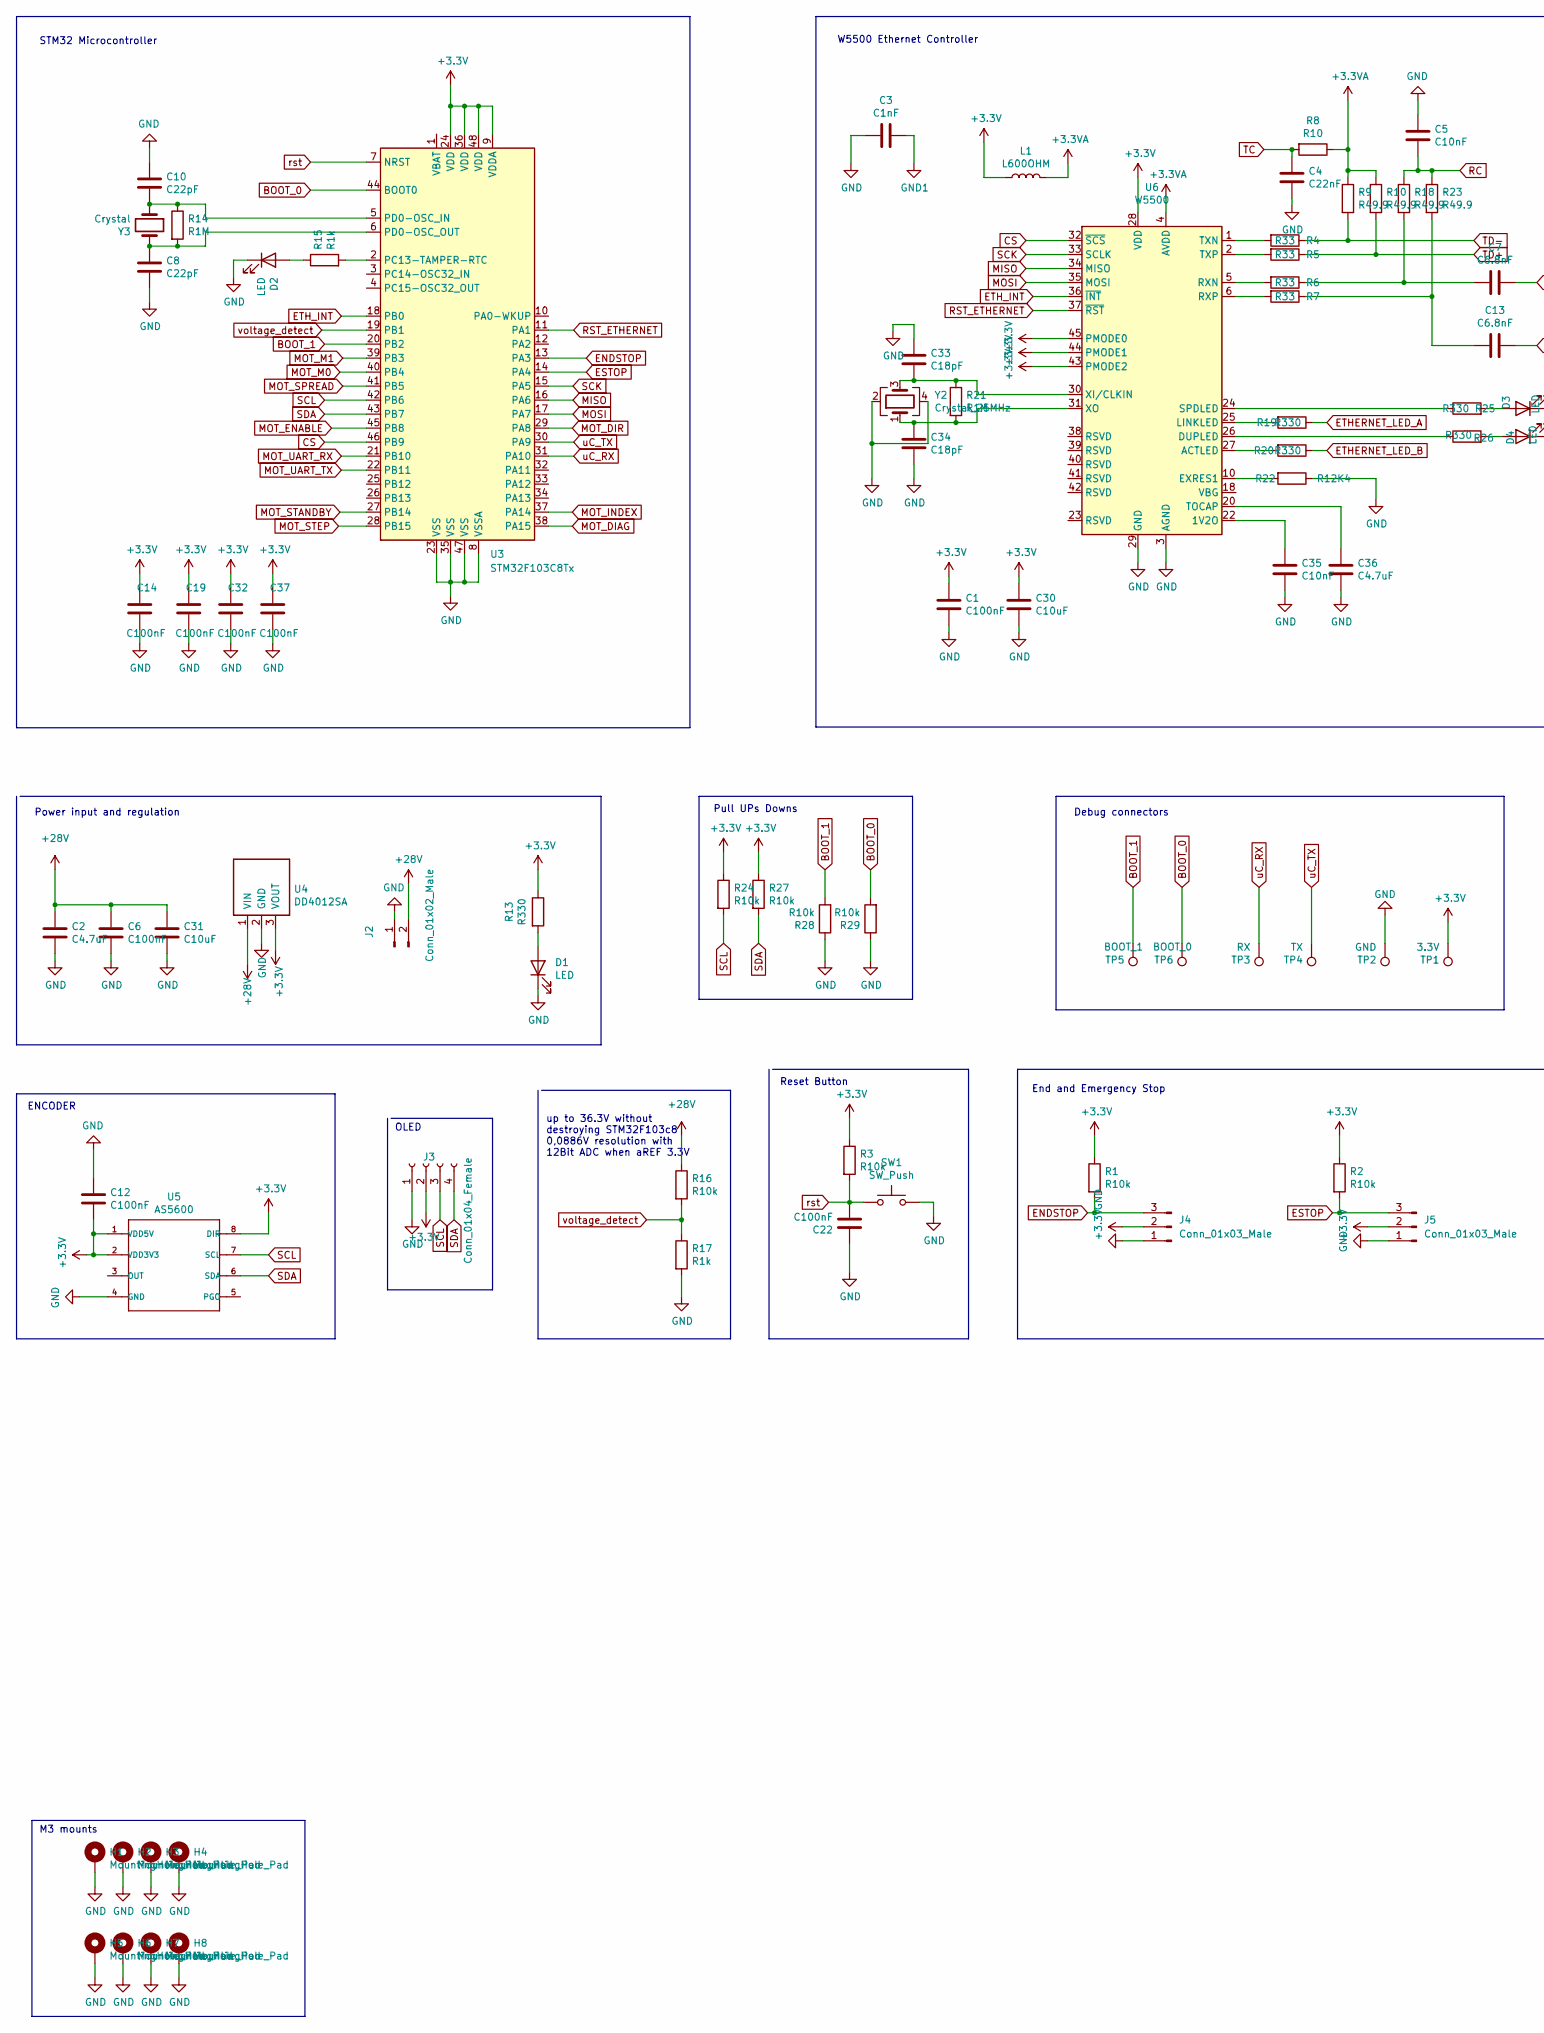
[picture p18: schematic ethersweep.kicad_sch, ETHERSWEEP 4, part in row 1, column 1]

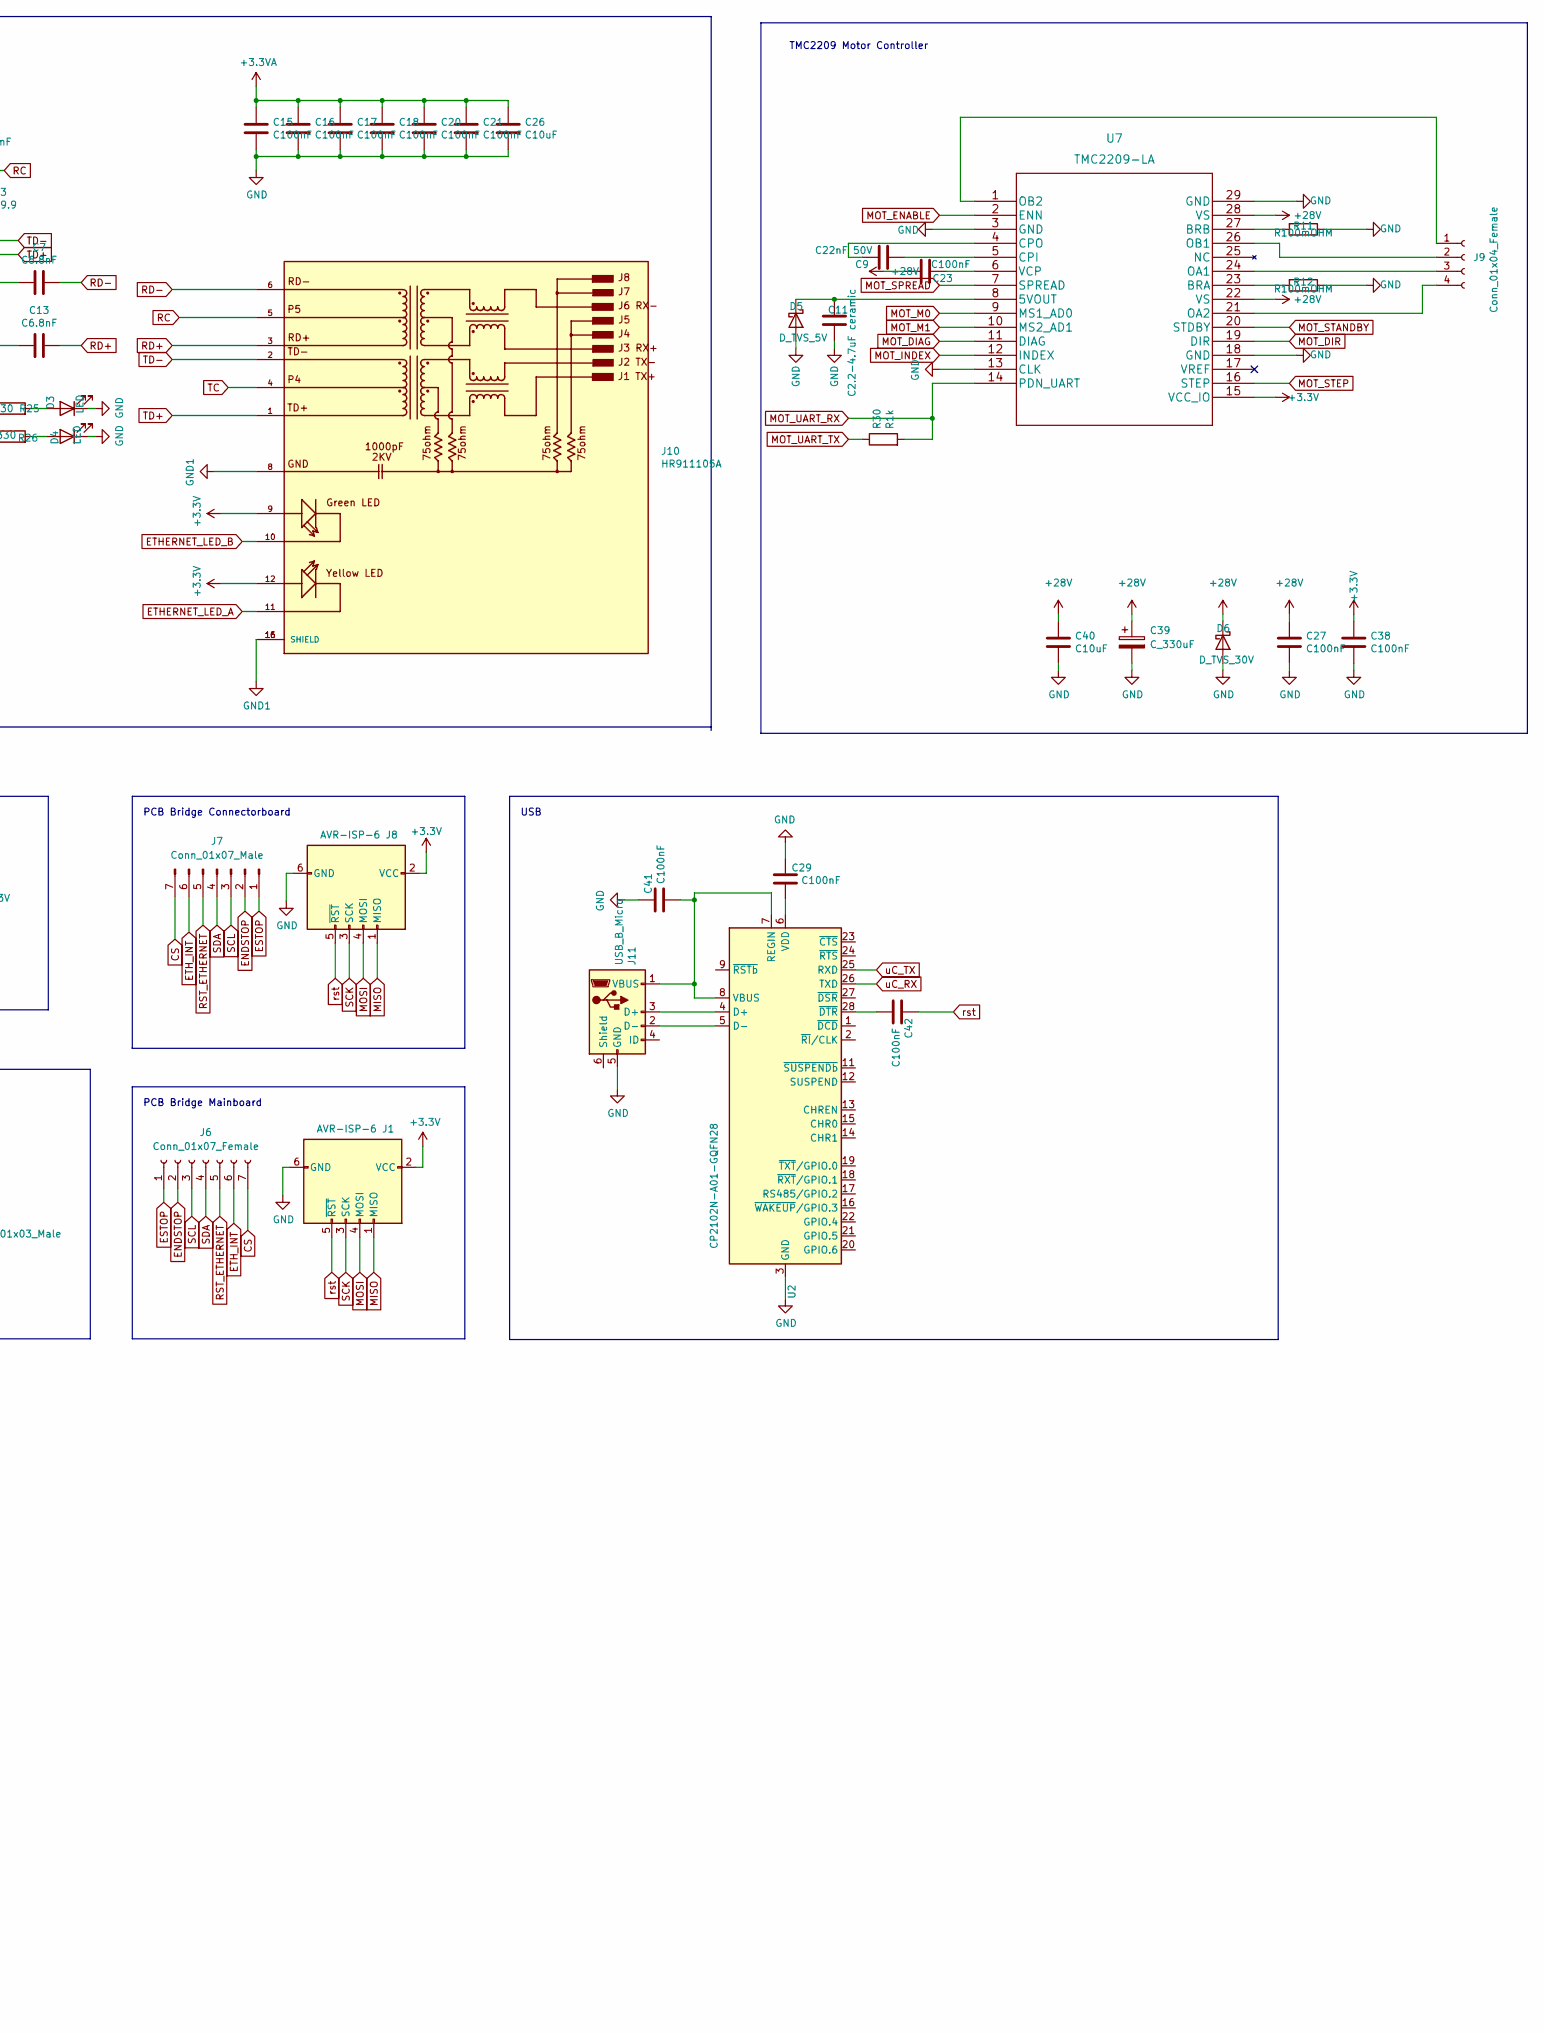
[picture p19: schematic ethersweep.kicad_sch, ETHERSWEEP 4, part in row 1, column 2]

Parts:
C1, C6, C23, C27, C38: C100nF; C_0603_1608Metric; LCSC C14663
C2: C4.7uF; C_1206_3216Metric; LCSC C29823
C3: C1nF; C_1206_3216Metric; LCSC C35216
C4: C22nF; C_0603_1608Metric; LCSC C21122
C5: C10nF; C_0603_1608Metric; LCSC C57112
C7, C13: C6.8nF; C_0402_1005Metric; LCSC C1542
C8, C10: C22pF; C_0402_1005Metric; LCSC C1555
C9: C22nF 50V; C_0402_1005Metric; LCSC C1532
C11: C2.2-4.7uF ceramic; C_1206_3216Metric; LCSC C29823
C12, C14, C15, C16, C17, C18, C19, C20, C21, C22, C29, C32, C37, C41, C42: C100nF; C_0402_1005Metric; LCSC C307331
C26, C30: C10uF; C_0805_2012Metric; LCSC C15850
C31, C40: C10uF; C_1206_3216Metric; LCSC C13585
C33, C34: C18pF; C_0402_1005Metric; LCSC C1549
C35: C10nF; C_0402_1005Metric; LCSC C15195
C36: C4.7uF; C_0402_1005Metric; LCSC C23733
C39: C_330uF; CP_Elec_10x10; LCSC C249985
D1, D2: LED; LED_0603_1608Metric; LCSC C2286
D3, D4: LED; LED_0603_1608Metric; LCSC C2296
D5: D_TVS_5V; D_SOD-123; LCSC C478011
D6: D_TVS_30V; D_SOD-123; LCSC C553410
H1, H2, H3, H4, H5, H6, H7, H8: MountingHole_Pad; MountingHole_3.2mm_M3_Pad_Via
J1, J8: AVR-ISP-6; IDC-Header_2x03_P2.54mm_Vertical
J2: Conn_01x02_Male; AMASS_XT30PW-M_1x02_P2.50mm_Horizontal; LCSC C431092
J3: Conn_01x04_Female; PinHeader_1x04_P2.54mm_Vertical
J4, J5: Conn_01x03_Male; JST_EH_S3B-EH_1x03_P2.50mm_Horizontal
J6: Conn_01x07_Female; PinHeader_1x07_P2.54mm_Vertical
J7: Conn_01x07_Male; PinHeader_1x07_P2.54mm_Vertical
J9: Conn_01x04_Female; JST_EH_S4B-EH_1x04_P2.50mm_Horizontal
J10: HR911105A; HANRUN_HR911105A; PARTREV A; LCSC C12074
J11: USB_B_Micro; USB_Micro-AB_Molex_47590-0001; LCSC C136001
L1: L600OHM; L_0805_2012Metric; LCSC C1017
R1, R2: R10k; R_0603_1608Metric; LCSC C25804
R3, R16, R24, R27, R28, R29: R10k; R_0402_1005Metric; LCSC C25744
R4, R5, R6, R7: R33; R_0603_1608Metric; LCSC C23140
R8: R10; R_0603_1608Metric; LCSC C22859
R9, R10, R18, R23: R49.9; R_0603_1608Metric; LCSC C23185
R11, R12: R100mOHM; R_2010_5025Metric; LCSC C175979
R13, R19, R20, R25, R26: R330; R_0603_1608Metric; LCSC C23138
R14, R21: R1M; R_0402_1005Metric; LCSC C26083
R15: R1k; R_0603_1608Metric; LCSC C21190
R17, R30: R1k; R_0402_1005Metric; LCSC C11702
R22: R12K4; R_0603_1608Metric; LCSC C234268
SW1: SW_Push; SW_SPST_B3U-3000P; LCSC C963349
TP1: 3.3V; TestPoint_Pad_D2.0mm
TP2: GND; TestPoint_Pad_D2.0mm
TP3: RX; TestPoint_Pad_D2.0mm
TP4: TX; TestPoint_Pad_D2.0mm
TP5: BOOT_1; TestPoint_Pad_D2.0mm
TP6: BOOT_0; TestPoint_Pad_D2.0mm
U2: CP2102N-A01-GQFN28; QFN-28-1EP_5x5mm_P0.5mm_EP3.35x3.35mm; LCSC C6568
U3: STM32F103C8Tx; LQFP-48_7x7mm_P0.5mm; LCSC C8734
U4: DD4012SA
U5: AS5600
U6: W5500; LQFP-48_7x7mm_P0.5mm; LCSC C32843
U7: TMC2209-LA; LCSC C465949
Y2: Crystal_25MHz; Crystal_SMD_3225-4Pin_3.2x2.5mm; LCSC C9006
Y3: Crystal; Crystal_SMD_5032-2Pin_5.0x3.2mm; LCSC C115962

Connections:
+3.3VA: C15.1, C16.1, C17.1, C18.1, C20.1, C21.1, C26.1, L1.2, R8.1, R9.1, R10.1, U6.4 (AVDD), U6.8 (AVDD), U6.11 (AVDD), U6.15 (AVDD), U6.17 (AVDD), U6.21 (AVDD)
+3V3: C1.1, C12.2, C14.1, C19.1, C30.1, C32.1, C37.1, C38.1, J1.2 (VCC), J3.2, J4.2, J5.2, J8.2 (VCC), J10.9, J10.12, L1.1, R1.1, R2.1, R3.1, R13.1, R24.1, R27.1, TP1.1, U3.9 (VDDA), U3.24 (VDD), U3.36 (VDD), U3.48 (VDD), U4.3 (VOUT), U5.1 (VDD5V), U5.2 (VDD3V3), U5.8 (DIR), U6.28 (VDD), U6.43 (PMODE2), U6.44 (PMODE1), U6.45 (PMODE0), U7.15 (VCC_IO); also elsewhere on the board
+28V: C2.1, C6.1, C23.1, C27.1, C31.1, C39.1, C40.1, D6.1 (K), J2.2, R16.1, U4.1 (VIN), U7.22 (VS), U7.28 (VS)
BOOT_0: R29.2, TP6.1, U3.44 (BOOT0); also elsewhere on the board
BOOT_1: R28.2, TP5.1, U3.20 (PB2)
CS: J6.7, J7.7, U3.46 (PB9), U6.32 (~SCS)
ENDSTOP: J4.3, J6.2, J7.2, R1.2, U3.13 (PA3)
ESTOP: J5.3, J6.1, J7.1, R2.2, U3.14 (PA4)
ETHERNET_LED_A: J10.11, R19.1
ETHERNET_LED_B: J10.10, R20.1
ETH_INT: J6.6, J7.6, U3.18 (PB0), U6.36 (~INT)
GND: C1.2, C2.2, C3.2, C4.1, C5.1, C6.2, C8.2, C10.1, C11.2, C12.1, C14.2, C15.2, C16.2, C17.2, C18.2, C19.2, C20.2, C21.2, C22.1, C26.2, C27.2, C29.1, C30.2, C31.2, C32.2, C33.1, C34.2, C35.2, C36.2, C37.2, C38.2, C39.2, C40.2, C41.1, D1.1 (K), D2.1 (K), D3.1 (K), D4.1 (K), D5.2 (A), D6.2 (A), H1.1, H2.1, H3.1, H4.1, H5.1, H6.1, H7.1, H8.1, J1.6 (GND), J2.1, J3.1, J4.1, J5.1, J8.6 (GND), J11.5 (GND), R11.1, R12.1, R17.2, R22.1, R28.1, R29.1, SW1.2, TP2.1, U2.3 (GND), U2.29 (GND), U3.8 (VSSA), U3.23 (VSS), U3.35 (VSS), U3.47 (VSS), U4.2 (GND), U5.4 (GND), U6.3 (AGND), U6.9 (AGND), U6.14 (AGND), U6.16 (AGND), U6.19 (AGND), U6.29 (GND), U6.48 (AGND), U7.3 (GND), U7.13 (CLK), U7.18 (GND), U7.29 (GND), Y2.2, Y2.4
GND1: C3.1, J10.8, J10.15 (SHIELD), J10.16 (SHIELD)
MISO: J1.1 (MISO), J8.1 (MISO), U3.16 (PA6), U6.34 (MISO)
MOSI: J1.4 (MOSI), J8.4 (MOSI), U3.17 (PA7), U6.35 (MOSI)
MOT_DIAG: U3.38 (PA15), U7.11 (DIAG)
MOT_DIR: U3.29 (PA8), U7.19 (DIR)
MOT_ENABLE: U3.45 (PB8), U7.2 (ENN)
MOT_INDEX: U3.37 (PA14), U7.12 (INDEX)
MOT_M0: U3.40 (PB4), U7.9 (MS1_AD0)
MOT_M1: U3.39 (PB3), U7.10 (MS2_AD1)
MOT_SPREAD: U3.41 (PB5), U7.7 (SPREAD)
MOT_STANDBY: U3.27 (PB14), U7.20 (STDBY)
MOT_STEP: U3.28 (PB15), U7.16 (STEP)
MOT_UART_RX: R30.2, U3.21 (PB10), U7.14 (PDN_UART)
MOT_UART_TX: R30.1, U3.22 (PB11)
unnamed: C7.2, R6.1, R18.2
unnamed: C13.2, R7.1, R23.2
unnamed: D1.2 (A), R13.2
unnamed: D2.2 (A), R15.1
unnamed: D3.2 (A), R25.2
unnamed: D4.2 (A), R26.2
unnamed: C11.1, D5.1 (K), U7.8 (5VOUT)
unnamed: J9.1, U7.1 (OB2)
unnamed: J9.2, U7.26 (OB1)
unnamed: J9.3, U7.24 (OA1)
unnamed: J9.4, U7.21 (OA2)
unnamed: J11.3 (D+), U2.4 (D+)
unnamed: J11.2 (D-), U2.5 (D-)
unnamed: C41.2, J11.1 (VBUS), U2.7 (REGIN), U2.8 (VBUS)
unnamed: C29.2, U2.6 (VDD)
unnamed: C42.2, U2.28 (~DTR)
unnamed: R15.2, U3.2 (PC13-TAMPER-RTC)
unnamed: C10.2, R14.1, U3.5 (PD0-OSC_IN), Y3.1
unnamed: C8.1, R14.2, U3.6 (PD0-OSC_OUT), Y3.2
unnamed: C35.1, U6.22 (1V2O)
unnamed: R20.2, U6.27 (ACTLED)
unnamed: R26.1, U6.26 (DUPLED)
unnamed: R22.2, U6.10 (EXRES1)
unnamed: R19.2, U6.25 (LINKLED)
unnamed: R6.2, U6.5 (RXN)
unnamed: R7.2, U6.6 (RXP)
unnamed: R25.1, U6.24 (SPDLED)
unnamed: C36.1, U6.20 (TOCAP)
unnamed: R4.2, U6.1 (TXN)
unnamed: R5.2, U6.2 (TXP)
unnamed: C33.2, R21.1, U6.30 (XI/CLKIN), Y2.3
unnamed: C34.1, R21.2, U6.31 (XO), Y2.1
unnamed: R12.2, U7.23 (BRA)
unnamed: R11.2, U7.27 (BRB)
unnamed: C9.2, U7.5 (CPI)
unnamed: C9.1, U7.4 (CPO)
unnamed: C23.2, U7.6 (VCP)
RC: C5.2, J10.5, R18.1, R23.1
RD+: C13.1, J10.3
RD-: C7.1, J10.6
RST_ETHERNET: J6.5, J7.5, U3.11 (PA1), U6.37 (~RST)
SCK: J1.3 (SCK), J8.3 (SCK), U3.15 (PA5), U6.33 (SCLK)
SCL: J3.3, J6.3, J7.3, R24.2, U3.42 (PB6), U5.7 (SCL)
SDA: J3.4, J6.4, J7.4, R27.2, U3.43 (PB7), U5.6 (SDA)
TC: C4.2, J10.4, R8.2
TD+: J10.1, R5.1, R10.2
TD-: J10.2, R4.1, R9.2
rst: C22.2, C42.1, J1.5 (~RST), J8.5 (~RST), R3.2, SW1.1, U3.7 (NRST)
uC_RX: TP3.1, U2.26 (TXD), U3.31 (PA10)
uC_TX: TP4.1, U2.25 (RXD), U3.30 (PA9)
voltage_detect: R16.2, R17.1, U3.19 (PB1)

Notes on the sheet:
USB
W5500 Ethernet Controller
M3 mounts
OLED
End and Emergency Stop
Power input and regulation
PCB Bridge Connectorboard
ENCODER
TMC2209 Motor Controller
Debug connectors
Pull UPs Downs
STM32 Microcontroller
up to 36.3V without destroying STM32F103c8 0,0886V resolution with 12Bit ADC when aREF 3.3V
Reset Button
PCB Bridge Mainboard

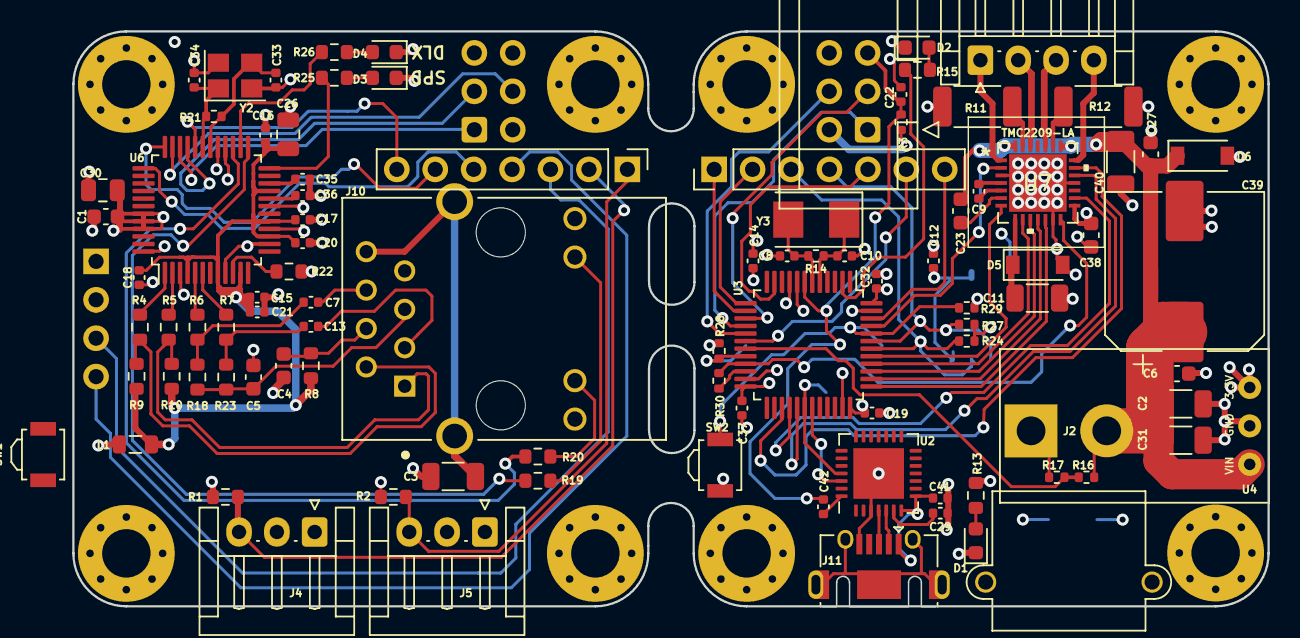
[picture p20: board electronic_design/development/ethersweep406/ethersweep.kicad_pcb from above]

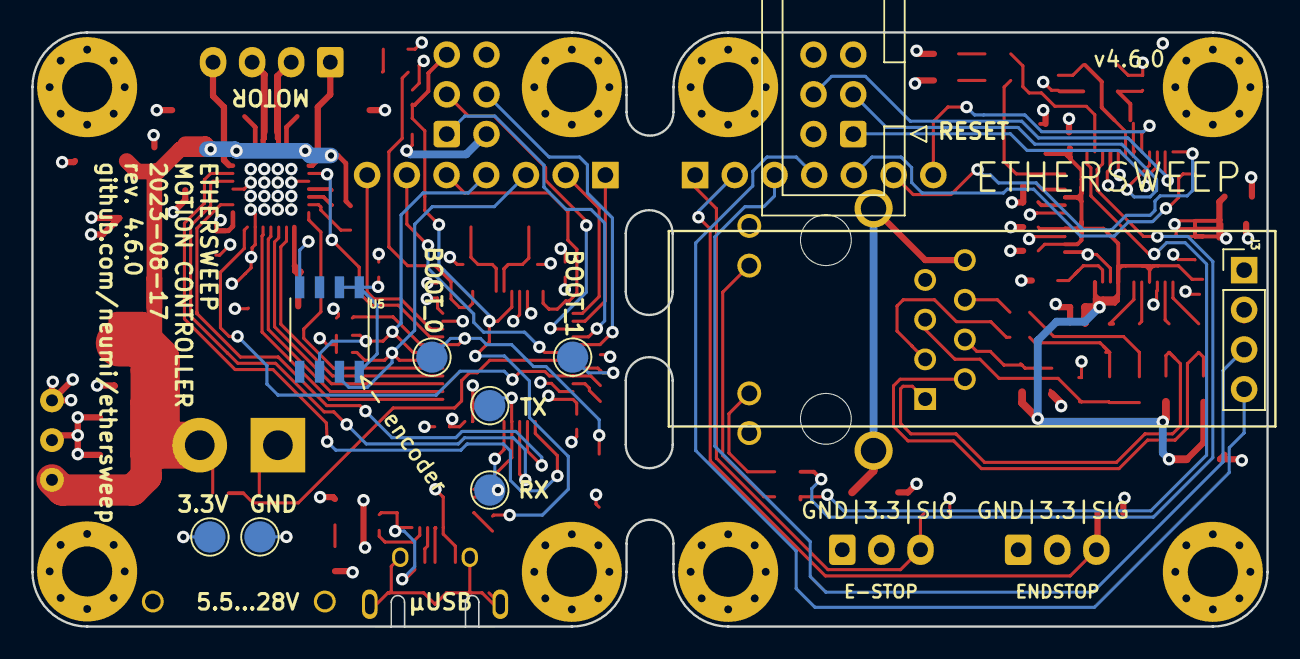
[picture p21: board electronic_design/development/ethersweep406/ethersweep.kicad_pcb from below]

Board: 4 copper layers, 79.0 x 38.0 mm, 111 parts (9 on the bottom side), 77 nets.

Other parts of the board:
SW2: SW_BOOT_0; SW_SPST_B3U-3000P

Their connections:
+3V3: SW2.1; also elsewhere on the board
BOOT_0: SW2.2; also elsewhere on the board

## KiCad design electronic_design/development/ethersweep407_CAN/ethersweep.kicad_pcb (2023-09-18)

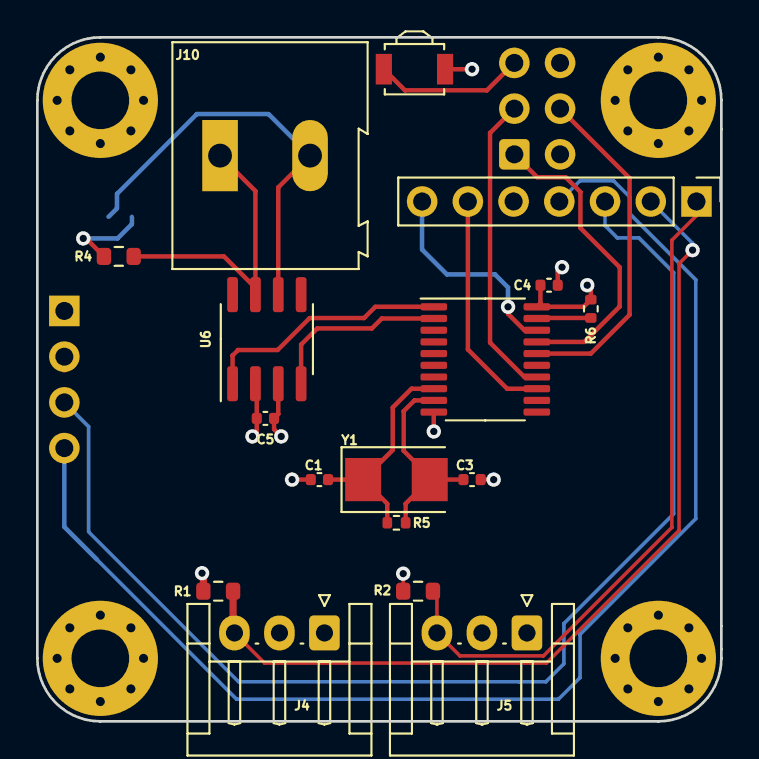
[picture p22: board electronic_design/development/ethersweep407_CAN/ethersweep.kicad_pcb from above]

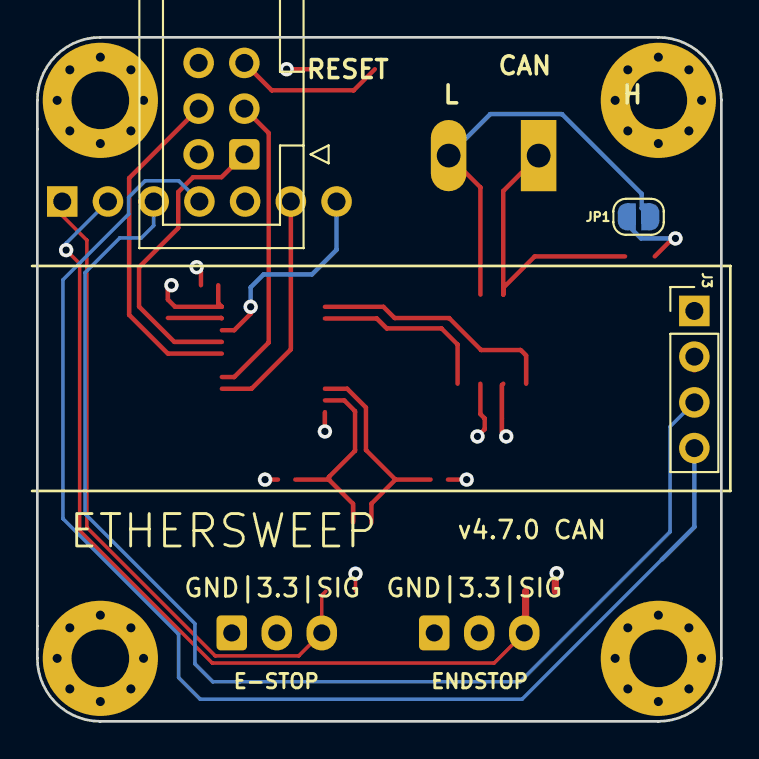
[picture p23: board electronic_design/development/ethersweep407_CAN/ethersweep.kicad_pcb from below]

Board: 4 copper layers, 38.0 x 38.0 mm, 24 parts (3 on the bottom side), 20 nets.

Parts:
C1, C3: C22pF; C_0402_1005Metric
C4, C5: C100nF; C_0402_1005Metric
H5, H6, H7, H8: MountingHole_Pad; MountingHole_3.2mm_M3_Pad_Via
J3: Conn_01x04_Female; PinHeader_1x04_P2.54mm_Vertical
J4, J5: Conn_01x03_Male; JST_EH_S3B-EH_1x03_P2.50mm_Horizontal
J7: Conn_01x07_Male; PinHeader_1x07_P2.54mm_Vertical
J8: AVR-ISP-6; IDC-Header_2x03_P2.54mm_Vertical
J10: CAN_BUS; TerminalBlock_Altech_AK300-2_P5.00mm
JP1: CAN_TERMINATION; SolderJumper-2_P1.3mm_Open_RoundedPad1.0x1.5mm
R1, R2: R10k; R_0603_1608Metric
R4: R120; R_0603_1608Metric
R5: R1M; R_0402_1005Metric
R6: R10k; R_0402_1005Metric
SW1: SW_Push; SW_SPST_B3U-3000P
U1: MCP2515-xST; TSSOP-20_4.4x6.5mm_P0.65mm
U6: TJA1051T-3; SOIC-8_3.9x4.9mm_P1.27mm
Y1: Crystal; Crystal_SMD_5032-2Pin_5.0x3.2mm

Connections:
+3V3: C4.1, C5.1, J3.2, J4.2, J5.2, J8.2 (VCC), R1.1, R2.1, R6.2, U1.20 (VDD), U6.3 (VCC)
CS: J7.7, U1.18 (~CS)
ENDSTOP: J4.3, J7.2, R1.2
ESTOP: J5.3, J7.1, R2.2
ETH_INT: J7.6, U1.13 (~INT)
GND: C1.1, C3.2, C4.2, C5.2, H5.1, H6.1, H7.1, H8.1, J3.1, J4.1, J5.1, J8.6 (GND), SW1.2, U1.10 (VSS), U6.2 (GND)
MISO: J8.1 (MISO), U1.17 (SO)
MOSI: J8.4 (MOSI), U1.16 (SI)
unnamed: J10.1, R4.2, U6.7 (CANH)
unnamed: J10.2, JP1.1 (A), U6.6 (CANL)
unnamed: JP1.2 (B), R4.1
unnamed: C3.1, R5.2, U1.9 (OSC1), Y1.2
unnamed: C1.2, R5.1, U1.8 (OSC2), Y1.1
unnamed: U1.2 (RXCAN), U6.4 (RXD)
unnamed: U1.1 (TXCAN), U6.1 (TXD)
unnamed: R6.1, U1.19 (~RESET)
SCK: J8.3 (SCK), U1.14 (SCK)
SCL: J3.3, J7.3
SDA: J3.4, J7.4
rst: J8.5 (~RST), SW1.1

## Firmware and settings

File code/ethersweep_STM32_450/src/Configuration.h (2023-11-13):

#pragma once

const String version = "3.5.2"; // software version

#define STATIC_IP 0 // when set 1, DHCP is enabled, when 0, statis IP is used

#define DEBUG_MODE 1 // when set 1, debugging output is enabled

#define BAUD_SPEED 9600 // debug and message baud speed

#define SYS_VOL 3.3 // system voltage in volts

#define OLED_I2C_ADDRESS 0x3C // i2c address of oled display

#define BUFFER_SIZE 256 // communication buffer size

#define LOCAL_PORT 8888 // local UDP port

#define STANDARD_REMOTE_SENSOR_PORT 5000 // remote machines receiving UDP port

#define DEFAULT_DISPLAY_REFRESH_TIME 100 // milliseconds until new data is shown
#define DEFAULT_FEEDBACK_TIME 300 // milliseconds until hearbeat


// action definitions
#define STEPS 0      // runs certain ammounts of steps
#define HOME 1       // homes until endstop is reached
#define RAMP 2       // ramps motor with certain slope
#define POWERCYCLE 3 // power cycles motor controller
#define POSITION 4   // encoder feedback position loop
#define SENSORFEEDBACK 5 // sends sensor values to IP and PORT
#define HEARTBEAT 6 // sends heartbeat answer values to IP and PORT
#define IDENTIFY 7 // sends IDENTIFY answer values to IP and PORT
#define CONFIGURE 8 // receives and saves configuration data

// scheduler modes
#define standby 0 // waiting for instructions
#define drive 1 // running drive loop
#define feedback 2 // feedback and hearbeat to host

// W5500 ethernet chip
#define SLEEP_PIN PB0 // ethernet int
#define RESET_PIN PA1 // ethernet reset
#define CS_PIN PB9 // ethernet chip select

// TMC2209 motor controller chip
#define ENABLE_PIN PB8
#define STEP_PIN PB15
#define DIR_PIN PA8
#define M0_PIN PB4 // MS1
#define M1_PIN PB3 // MS2
#define DIAG_PIN PA15
#define FAULT_PIN PA14

// sensor inputs
#define VOLT_DETECT_PIN PB1
#define END_STOP_PIN PA3
#define E_STOP_PIN PA4
#define RANDOM_SEED_PIN PA2

// outputs
#define LED_PIN PC13

// connection modes
#define CONNECTION_STAT "STAT"
#define CONNECTION_DHCP "DHCP"
#define CONNECTION_USB "USB "
 

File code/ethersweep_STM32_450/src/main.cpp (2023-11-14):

// FOR HARDWARE 4.5.0 for STM32F103C8T6 and TMC2209 controller
#include <Arduino.h>
#include <SPI.h>
#include <Ethernet.h>
#include <EthernetUdp.h>
#include <IPAddress.h>
#include <ArduinoJson.h>
#include <Wire.h>
#include <EEPROM.h>
#include "Configurator.h"
#include "SSD1306Ascii.h"
#include "SSD1306AsciiWire.h"
#include "Configuration.h"
#include "Connection.h"
#include "SensorManager.h"
#include "Motor.h"
#include "Display.h"
#include "Messenger.h"


#if STATIC_IP
String connectionMode = CONNECTION_STAT;
IPAddress ip(192, 168, 1, 111); // static IP
#else
String connectionMode = CONNECTION_DHCP;
IPAddress ip(0, 0, 0, 0);
#endif

SSD1306AsciiWire oled;
AMS_5600 ams5600;
EthernetUDP Udp;

SensorManager sensorManager(&ams5600, E_STOP_PIN, END_STOP_PIN, DIAG_PIN, FAULT_PIN, VOLT_DETECT_PIN);
Connection connection(RANDOM_SEED_PIN);
Display display(&sensorManager, &oled, &connection);
Motor motor(&sensorManager, &display, STEP_PIN, DIR_PIN, ENABLE_PIN, M0_PIN, M1_PIN, LED_PIN);
Messenger messenger(&Serial1);
Configurator configurator;

int action = 0;
int motorSpeed = 0;
int motorSlope = 0;
int motorSteps = 0;
byte motorStepMode = 0;
bool motorDirection = false;
bool motorHold = false;
double degrees = 0.0;

IPAddress sensorDestinationIp(0, 0, 0, 0);     // IP to send sensor data to
int sensorPort = STANDARD_REMOTE_SENSOR_PORT;

bool usbActive = false;

unsigned long previousDisplayMillis;
unsigned long previousNetworkMillis;
unsigned long previousSensorMillis;
unsigned long previousMotorMillis;
unsigned long previousFeedbackMillis;

int displayRefreshTime;
int feedbackTime;

// ETHERNET & UDP
char packetBuffer[BUFFER_SIZE]; // buffer to hold incoming UDP packet
StaticJsonDocument<BUFFER_SIZE> doc;

int schedulerMode = 0;


void setup()
{
  Wire.begin();

  connection.setConnectionMode(connectionMode);
  messenger.init(BAUD_SPEED);
  configurator.loadData();
  
  displayRefreshTime = configurator.getDisplayRefreshTime();
  feedbackTime = configurator.getFeedbackTime();
  
  messenger.sendInfo("Ethersweep " + version);

  if (sensorManager.startUpCheck(messenger))
  {
    messenger.sendInfo(F("Sensors OK"));
  }
  else
  {
    messenger.sendError(F("Sensor fail"));
  }

  connection.getMac();
  display.setupDisplay();
  motor.disableMotor();

  Serial1.setTimeout(10);

  if (Serial1.available() > 0)
  {
    usbActive = true;
    connectionMode = CONNECTION_USB;
  }
  else
  {
    Ethernet.init(CS_PIN);
#if STATIC_IP
    Ethernet.begin(connection.mac, ip);
    if (Ethernet.hardwareStatus() == EthernetNoHardware)
    {
      messenger.sendError(F("Ethernet error"));
    }
    if (Ethernet.linkStatus() == LinkOFF)
    {
      messenger.sendError(F("Ethernet no link"));
    }
    messenger.sendInfo(F("Ethernet OK"));
#else
    if (Ethernet.begin(connection.mac) == 0)
    {
      if (Ethernet.hardwareStatus() == EthernetNoHardware)
      {
        messenger.sendError(F("Ethernet error"));
      }
      if (Ethernet.linkStatus() == LinkOFF)
      {
        messenger.sendError(F("Ethernet no link"));
      }
      Ethernet.begin(connection.mac, ip);
    }
    else
    {
      messenger.sendInfo(F("Ethernet OK"));
    }
#endif
    Udp.begin(LOCAL_PORT);
  }

  display.initializeDisplay(Ethernet.localIP());

  messenger.sendInfo("IP: " + display.formatAddress(Ethernet.localIP()));
  messenger.sendInfo(F("done"));
}

void loop()
{
  if(schedulerMode == standby) 
  {
  }
  else if (schedulerMode == drive)
  {
  }
  else if (schedulerMode == feedback)
  {
  }

  sensorManager.getEmergencyStopState();
  sensorManager.getEndStopState();

  if (usbActive)
  {
    if (Serial.available() > 0)
    {
      Serial.readStringUntil('\n').toCharArray(packetBuffer, BUFFER_SIZE);
      sensorManager.setJobState(false);
    }
  }
  else
  {
    int packetSize = Udp.parsePacket();
    if (packetSize)
    {
      Udp.read(packetBuffer, BUFFER_SIZE);
      sensorManager.setJobState(false);
    }
  }

  if (millis() - previousDisplayMillis >= displayRefreshTime)
  {
    display.drawDisplay();
    previousDisplayMillis = millis();
  }

  if (!sensorManager.getJobState())
  {
    DeserializationError error = deserializeJson(doc, packetBuffer, BUFFER_SIZE);
    if (error)
    {
      messenger.sendError(F("JSON error"));
    }
    else
    {
        /**
         * data scheme 
          {
          "mode": "configuration",
            "action": {
              "displayRefresh": 50,
              "feedbackTime": 200,
              "connectionMode": "wifi"
            },
            "executionTime": 1636986000000000
          }
         * 
        */

      action = doc["mode"];
      motorSteps = doc["steps"];
      motorSpeed = doc["speed"];
      motorSlope = doc["slope"];
      motorDirection = doc["direction"];
      motorStepMode = doc["stepmode"];
      motorHold = doc["hold"];

      if (doc.containsKey("degrees")) {
        degrees = doc["degrees"];
      }

      if (doc.containsKey("port")) {
        sensorPort = doc["port"];
      }
      
      if (doc.containsKey("ip")) {
        const char* ipAddressStr = doc["ip"];
        sensorDestinationIp.fromString(ipAddressStr);
      }
      else {
        sensorDestinationIp = Udp.remoteIP();
      }

      switch (action)
      {
      case STEPS:
        motor.driveMotor(motorSteps, motorSpeed, motorDirection, motorStepMode, motorHold);
        break;
      case HOME:
        motor.homeMotor(motorSteps, motorSpeed, motorDirection, motorStepMode, motorHold);
        break;
      case RAMP:
        motor.rampMotor(motorSteps, motorSpeed, motorSlope, motorDirection, motorStepMode, motorHold);
        break;
      case POSITION:
        motor.positionMotor(degrees);
        break;
      case SENSORFEEDBACK:
        motor.sensorFeedback(sensorDestinationIp, sensorPort, messenger, Udp);
        break;
      case HEARTBEAT:
        motor.sendHeartbeat(sensorDestinationIp, sensorPort, messenger, Udp);
        break;
      case IDENTIFY:
        motor.identify(sensorDestinationIp, sensorPort, messenger, Udp);
        break;
      case CONFIGURE:
        configurator.processNewConfiguration();
        break;
      case POWERCYCLE:
        motor.powerCycleMotor();
        break;
      }
    }

    sensorManager.setJobState(true);
  }
}

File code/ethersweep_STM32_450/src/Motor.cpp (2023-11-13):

#include "Motor.h"
#include <ArduinoJson.h>
#include "Configuration.h"




Motor::Motor(SensorManager *sensor, Display *display, byte stepPin, byte dirPin, byte enablePin, byte m0Pin, byte m1Pin, byte ledPin)
{
    this->sensor = sensor;
    this->display = display;
    this->stepPin = stepPin;
    this->dirPin = dirPin;
    this->enablePin = enablePin;
    this->m0Pin = m0Pin;
    this->m1Pin = m1Pin;
    this->ledPin = ledPin;

    init();
}

// inits all outputs.
void Motor::init()
{
    pinMode(this->stepPin, OUTPUT);
    pinMode(this->dirPin, OUTPUT);
    pinMode(this->enablePin, OUTPUT);
    pinMode(this->m0Pin, OUTPUT);
    pinMode(this->m1Pin, OUTPUT);
    pinMode(this->ledPin, OUTPUT);

    digitalWrite(this->stepPin, LOW);
}

// sets step mode. options are half, quater, eigth and sixteenth step mode.
void Motor::setStepMode(byte mode)
{
    switch (mode)
    {
    // TMC2208 MS0, MS1: 10: 1/2, 01: 1/4, 00: 1/8, 11: 1/16
    // TMC2209 M1, M0: 00: 1/8, 01: 1/32, 10: 1/64 11: 1/16
    case 8:
        digitalWrite(this->m0Pin, LOW);
        digitalWrite(this->m1Pin, LOW);
        break;
    case 16:
        digitalWrite(this->m0Pin, HIGH);
        digitalWrite(this->m1Pin, HIGH);
        break;
    case 32:
        digitalWrite(this->m0Pin, HIGH);
        digitalWrite(this->m1Pin, LOW);
        break;
    case 64:
        digitalWrite(this->m0Pin, LOW);
        digitalWrite(this->m1Pin, HIGH);
        break;
    default: // defaults to 1/64
        digitalWrite(this->m0Pin, LOW);
        digitalWrite(this->m1Pin, HIGH);
        break;
    }
}

// drives motor a certain number of steps.
void Motor::driveMotor(int motorSteps, int motorSpeed, bool motorDirection, byte motorStepMode, bool hold)
{
    this->display->drawDisplay();

    digitalWrite(this->ledPin, HIGH);
    if (!this->sensor->getEmergencyStopState())
    {
        this->enableMotor();
        this->setStepMode(motorStepMode);
        if (motorDirection == 1)
        {
            digitalWrite(this->dirPin, HIGH);
        }
        else if (motorDirection == 0)
        {
            digitalWrite(this->dirPin, LOW);
        }
        motorSpeed = constrain(motorSpeed, 0, 10000);
        for (int i = 0; i < motorSteps; i++)
        {
            if (this->sensor->getEmergencyStopState())
            {
                this->disableMotor();
                break;
            }
            digitalWrite(this->stepPin, LOW);
            delayMicroseconds(motorSpeed);
            digitalWrite(this->stepPin, HIGH);
            delayMicroseconds(motorSpeed);
        }
        if (hold == 0)
        {
            this->disableMotor();
        }
    }
    digitalWrite(this->ledPin, LOW);
}

// ramps motor to speed. Ramp of 10 % means 5% acceleration, 90% running full speed and 5% decelleration.
void Motor::rampMotor(int motorSteps, int motorSpeed, int motorSlope, bool motorDirection, byte motorStepMode, bool hold)
{
    this->display->drawDisplay();
    digitalWrite(this->ledPin, HIGH);

    float speedCorrection = 0.0;

    this->enableMotor();
    this->setStepMode(motorStepMode);

    if (motorDirection == 1)
    {
        digitalWrite(this->dirPin, HIGH);
    }
    else if (motorDirection == 0)
    {
        digitalWrite(this->dirPin, LOW);
    }
    motorSpeed = constrain(motorSpeed, 0, 10000);
    float slopeSteps = motorSteps / (100 / motorSlope) / 2.0;

    for (int i = 0; i < motorSteps; i++)
    {
        if (slopeSteps > i)
        {
            speedCorrection = (slopeSteps - i) / slopeSteps;
        }
        if (i > motorSteps - slopeSteps)
        {
            speedCorrection = 1.0 - ((motorSteps - i) / slopeSteps);
        }
        if (this->sensor->getEmergencyStopState())
        {
            this->disableMotor();
            break;
        }
        digitalWrite(this->stepPin, LOW);
        delayMicroseconds(motorSpeed + round(motorSpeed * speedCorrection));
        digitalWrite(this->stepPin, HIGH);
        delayMicroseconds(motorSpeed + round(motorSpeed * speedCorrection));
    }
    if (hold == 0)
    {
        this->disableMotor();
    }

    digitalWrite(this->ledPin, LOW);
}

// homes motor until endstop is pressed. After first End Stop hit, moves back and tries again slower.
void Motor::homeMotor(int motorSteps, int motorSpeed, bool motorDirection, byte motorStepMode, bool hold)
{
    int homingState = 0;
    const int homing_runs = 3;
    while (true)
    {
        if (homingState == homing_runs)
        {
            break;
        }
        if (this->sensor->getEmergencyStopState())
        {
            this->disableMotor();
            break;
        }

        if (this->sensor->getEndStopState())
        {
            if (homingState < homing_runs - 1)
            {
                driveMotor(motorSteps, motorSpeed * (homingState + 1), !motorDirection, motorStepMode, 1);
            }
            homingState += 1;
        }
        driveMotor(1, motorSpeed * (2 * homingState + 1), motorDirection, motorStepMode, 1);
    }
}

void Motor::positionMotor(double degrees) {

    byte stepMode = 32;

    float currAngle = this->sensor->getAngle();
    float errorAngle = currAngle - degrees;
    
    while (abs(errorAngle) > 0.1) {
        currAngle = this->sensor->getAngle();
        errorAngle = currAngle - degrees;

        // 16 * 200 steps / rev = 8,888 steps / deg
        int correctionSteps = round(abs(errorAngle) * 8.8888);
        int correctionSpeed = 10000 - correctionSteps;
        Serial1.print(correctionSpeed);
        Serial1.print(",");
        Serial1.println(correctionSteps);

        if (errorAngle > 0) { // run left
        this->driveMotor(correctionSteps, 100, 1, stepMode, 0);
        }
        else if (errorAngle < 0) { // run right
        this->driveMotor(correctionSteps, 100, 0, stepMode, 0);
        }
    }
    
    //this->disableMotor();
}

// sends sensor data to ip, port
void Motor::sensorFeedback(IPAddress ip, int port, Messenger messenger, EthernetUDP udp) {
    const size_t capacity = 256;
    DynamicJsonDocument jsonDoc(capacity);

    // Populate JSON object with sensor data
    jsonDoc["eStop"] = this->sensor->getEmergencyStopState();
    jsonDoc["endStop"] = this->sensor->getEndStopState();
    jsonDoc["motorDiagnose"] = this->sensor->getMotorDriverDiagnose();
    jsonDoc["motorFailure"] = this->sensor->getMotorDriverFailure();
    jsonDoc["jobState"] = this->sensor->getJobState();
    jsonDoc["angle"] = this->sensor->getAngle();
    jsonDoc["voltage"] = this->sensor->getVoltage();
    jsonDoc["version"] = version;

    String message;
    serializeJson(jsonDoc, message);

    // sends UDP message
    messenger.sendUDPMessage(ip, port, message, udp);

}
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

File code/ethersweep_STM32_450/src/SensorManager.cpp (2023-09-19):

#include "SensorManager.h"
#include "Messenger.h"


SensorManager::SensorManager(AMS_5600 *ams5600, byte eStopPin, byte endStopPin, byte diagPin, byte faultPin, byte voltDetectPin)
{
    
    this->eStopPin = eStopPin;
    this->endStopPin = endStopPin;
    this->diagPin = diagPin;
    this->faultPin = faultPin;
    this->voltDetectPin = voltDetectPin;
    this->jobDone = true;
    this->ams5600 = ams5600;

    init();
}

void SensorManager::init()
{
    pinMode(this->eStopPin, INPUT);
    pinMode(this->endStopPin, INPUT);
    pinMode(this->diagPin, INPUT);
}

void SensorManager::readSensorValues()
{
    this->voltage = getVoltage();
    this->angle = getAngle();
    this->magnet = checkMagnet();
    this->emergencyStop = getEmergencyStopState();
    this->endStop = getEndStopState();
    this->motorDriverDiagnose = getMotorDriverDiagnose();
    this->motorDriverFailure = getMotorDriverFailure();
    this->jobDone = getJobState();
}

bool SensorManager::startUpCheck(Messenger messenger)
{
    messenger.sendInfo("Startup check running...");
    this->readSensorValues();

    if (motorDriverDiagnose == 1)
    {
        messenger.sendError("Mot Diag");
        return false;
    }

    if (motorDriverFailure == 1)
    {
        messenger.sendError("Mot Driver");
        return false;
    }

    if (magnet == 0)
    {
        messenger.sendError("Magnet");
        return false;
    }
    if (voltage < 5.0)
    {
        messenger.sendError("Voltage");
        return false;
    }
    return true;
}

// return voltage in millivolts
int SensorManager::getVoltage()
{
    int vin = (analogRead(this->voltDetectPin) * 3.3) / 1024.0 / (1.0 / 11.0) * 1000;
    return vin;
}

float SensorManager::getAngle()
{
    float rawAngle = this->ams5600->getRawAngle();
    
    /* Raw data reports 0 - 4095 segments, which is 0.087890625 of a degree */
    float normalizedAngle = (rawAngle * 360.0) / 4096.0;

    return normalizedAngle;
}

bool SensorManager::checkMagnet()
{
    if (this->ams5600->detectMagnet() == 0)
    {
        while (1)
        {
            if (this->ams5600->detectMagnet() == 1)
            {
                return true;
            }
            else
            {
                // debugPrintln("magnet err");
            }
            delay(100);
        }
    }
    return true;
}

bool SensorManager::getEmergencyStopState()
{
    return !digitalRead(this->eStopPin); // Emergency Stop pressed if HIGH
}

bool SensorManager::getEndStopState()
{
    return !digitalRead(this->endStopPin); // END Stop pressed if HIGH
}

bool SensorManager::getMotorDriverDiagnose()
{
    return digitalRead(this->diagPin); // Motor driver diagnose if HIGH
}

bool SensorManager::getMotorDriverFailure()
{
    return digitalRead(this->faultPin); // Motor driver failure if HIGH
}

bool SensorManager::getJobState() // Running job state reuturns TRUE when in idle
{
    return this->jobDone;
}

bool SensorManager::setJobState(bool state) // sets job state running 0 or idle 1
{
    return this->jobDone = state;
}

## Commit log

2020-04-13 added initial
    [ethersweep-B.CrtYd.gbr, ethersweep-B.Cu.gbr, ethersweep-B.Fab.gbr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]
2020-07-04 added i2c oled display support
2020-07-10 added i2c display support
2021-11-09 added 304 version
    [atmega328_3_3V.sch, drv8825_stepper_motor_controller.sch, enc28j60_ethernet_controller.sch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]
2022-03-23 added 3d cad files, production files, for 3.0.4
    [ethersweep-B_Courtyard.gbr, ethersweep-B_Cu.gbr, ethersweep-B_Fab.gbr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]
2022-04-10 minor electronics changes, DHCP standard enabled, display optimizations, speed improvements in main loop, display refresh only with empty ethernet buffer
    [ethersweep.kicad_pcb]
2022-07-25 current version, dhcp standard enabled, fast display refresh,
2022-07-25 removed old arduino code
2022-07-25 removed old code + design files
    [atmega328_3_3V.sch, drv8825_stepper_motor_controller.sch, enc28j60_ethernet_controller.sch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]
2022-07-26 added 3d files and documentation images
    [ethersweep304.FCStd]
2022-09-02 added / fixed power cycle. strange problem with random step mode changes occoured. probable ram issue
2022-09-05 added servo feature test
2022-09-14 angle and voltage display corrected fixes #6
2022-09-16 Create FUNDING.yml
    added funding button
2022-09-16 styling, simplified voltage calculation
2022-09-20 added arduinojson version comment
2022-09-21 added arduino json version 6 support
2022-09-29 usb mode bug fix when no LAN cable is connected
2022-09-29 changed pinout for nema17 motor to be parallel to connector
    [ethersweep.kicad_pcb, ethersweep.kicad_sch]
2022-10-16 minor changes
    [ethersweep.kicad_pcb]
2022-11-18 added OOP code, platformio config and project. Major refactoring done
    [Configuration.h]
2022-11-20 minor bug fixes, cleanup, restructuring
    [Configuration.h]
2022-12-12 added test, unity setup and config and some minor changes
    [Configuration.h]
2022-12-12 first changes for stm32 and tmc2209 transfer
    [ethersweep.kicad_pcb, ethersweep.kicad_sch, ethersweep.sch]
2023-01-10 major commit for ethersweep 4 with STM32 MCU and USB C + fixes
    [ethersweep.kicad_pcb, ethersweep.kicad_sch]
2023-01-11 cleanup, schmeatic design around USB connecotr, STM32 and reorganisation
    [ethersweep.kicad_pcb, ethersweep.kicad_sch]
2023-01-12 layout version 4 in manufacturable state: STM32, TMC2209, USBC, 3 pin switches
    [ethersweep.kicad_pcb, ethersweep.kicad_sch]
2023-01-16 minor design changes
    [ethersweep.kicad_pcb, ethersweep.kicad_sch]
2023-01-24 pcb design changes, reorganisation, JLC part number assignments, size corrections
    [ethersweep.kicad_pcb, ethersweep.kicad_sch]
2023-01-24 added production data
    [ethersweep-B_Courtyard.gbr, ethersweep-B_Cu.gbr, ethersweep-B_Fab.gbr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]
2023-01-24 part assignments, minor part changes
    [ethersweep.kicad_pcb, ethersweep.kicad_sch]
2023-02-08 added 3d files for v4
    [ethersweep.kicad_pcb, ethersweep401_full_assembly.FCStd, top_case_cnc.FCStd]
2023-03-08 board fixes for 402 version
    [ethersweep.kicad_pcb]
2023-03-08 added 402 version
    [HR911105A.step, HRO_TYPE-C-31-M-12.step, TMC2209.STEP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]
2023-03-08 added development and production
    [HR911105A.step, HRO_TYPE-C-31-M-12.step, TMC2209.STEP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]
2023-05-24 added version 405 files for tmc2209 version with micro usb and CP2102 chip. production ready
    [HR911105A.step, HRO_TYPE-C-31-M-12.step, TMC2209.STEP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]
2023-06-06 added getting started initial. plus code to test the TMC2209 via serial2 on the STM32
2023-06-06 added board setting images
2023-06-07 added code for stm32 version for hardware 4.5
    [Configuration.h]
2023-06-07 Update README.md
    added news for stm32 version
2023-08-17 added latest production and development version
    [HR911105A.step, HRO_TYPE-C-31-M-12.step, TMC2209.STEP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]
2023-08-17 removed old production
    [ethersweep-B_Courtyard.gbr, ethersweep-B_Cu.gbr, ethersweep-B_Fab.gbr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]
2023-09-18 added CAN development board
    [HR911105A.step, HRO_TYPE-C-31-M-12.step, TMC2209.STEP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]
2023-09-18 added sensor feedback mode, refactoring
    [Configuration.h]
2023-09-19 changed voltage to millivolts
2023-10-24 added heartbeat mode
    [Configuration.h]
2023-10-25 added identify mode and minor changes
    [Configuration.h]
2023-10-25 cleanup in software dir
    [Configuration.h]
2023-10-25 cleanup 3d files
    [ethersweep304.FCStd, ethersweep401_assembly.FCStd, top_case_cnc.FCStd]
2023-10-25 removed old stl file
2023-10-25 removed 405 version from development dir
    [HR911105A.step, HRO_TYPE-C-31-M-12.step, TMC2209.STEP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]
2023-10-25 cleanup and minor design changes in 406
    [ethersweep.kicad_pcb, ethersweep.kicad_sch]
2023-11-13 added dynamic configuration concept
    [Configuration.h]

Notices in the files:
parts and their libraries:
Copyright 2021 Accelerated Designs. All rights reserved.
